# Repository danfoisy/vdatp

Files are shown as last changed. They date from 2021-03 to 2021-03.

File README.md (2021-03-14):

# VDATP
## Volumetric Display using an Acoustically Trapped Particle

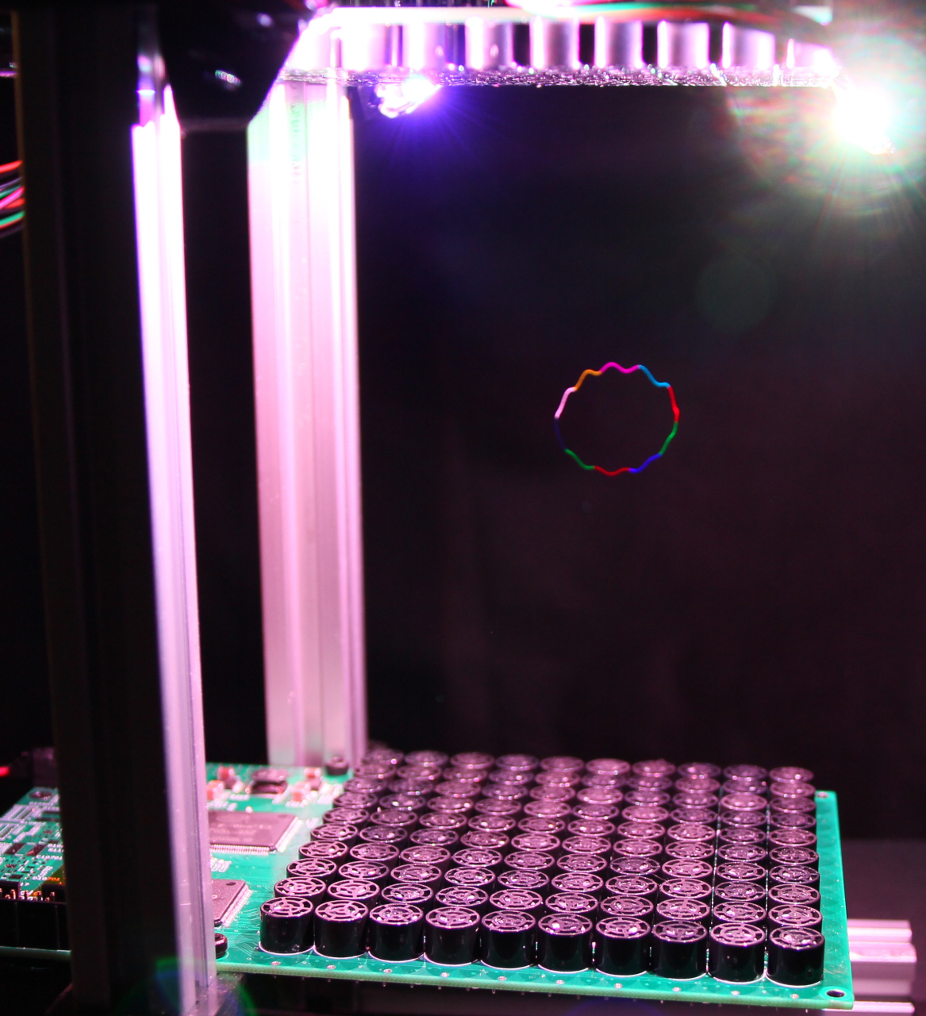
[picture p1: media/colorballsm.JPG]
VDATP video


This was such a fun project - I still giggle (maniacally) when watching this thing go.  There's something truly magical about watching something levitate in mid-air and then start zipping around so fast, you can't see it.  In any case, I hope these project files help someone!

Video: https://www.youtube.com/watch?v=hCC1C5KIeUA

References:
- PhysicsGirl acoustic levitator: https://www.youtube.com/watch?v=ABjRnSYw-4k
- Acoustic levitator Instructable: https://www.instructables.com/Acoustic-Levitator/
- University of Sussex video: https://www.youtube.com/watch?v=Tm8JRlJ1q50
- University of Sussex paper: http://sro.sussex.ac.uk/id/eprint/86930/

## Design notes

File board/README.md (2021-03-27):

# Board

Herein lives the Kicad schedmatics, PCB and BOM files.  If looking to replicate, I highly recommend you look at `errata.txt` for a list of mistakes I made that should be fixed on the next spin of the board.

Some notes:
- SPI goes to all 4 FPGAs simultaneously.  MISO is not used
- there are jumpers in place to allow the board to operate with only one FPGA installed (and only 50 transducers) but to run both FPGAs, the following jumpers must be configured:
-- R122, R123, R124, R126, R127, R128 <= populated
-- R125, R129 <= not populated
-- R105, R111, R113 <= not populated
-- R112 <= populated
- Raspberry Pi W installed on top board only. Top board needs 5V DC/DC converter populated, leave unpopulated on bottom board
-- Rasberry Pi header soldered on backside of Pi 
- U101 and U102 are soldered on top board (note errata on U101). Only U101 populated on bottom board
-- only simple twisted pair required for each RS485 connection
- LEDs only connect on top board (populate LED drivers and connectors)
- each board requires a max of 2A at 24V. No power sequencing required
- to allow the config device to program the FPGAs
-- JP201/JP202 must be left unpopulated
-- JP11001/JP11002 must be cut and msel0/1 must be connected to ground with jumper
- each FPGA must have jumpers configured to tell it which transducers it is responsible for
-- top board: populate R11004
-- bottom board: populate R11003, R203, R204
- original ultrasonic transducer is no available on aliexpress but https://manorshi.en.alibaba.com/product/60248714908-801018150/Manorshi_10mm_40khz_piezo_ultrasonic_Transmitter_Receiver_sensor.html should work but I've not tested (make sure to order the transmitter version)
- distance between boards is not super critical - mine are set up 145mm apart but other distance work just as well
- FPGAs can be programmed with a USB blaster type device.  I use https://www.terasic.com.tw/cgi-bin/page/archive.pl?Language=English&No=46
-- all FPGAs get the same program
- the transducers have a polarity marked on them - but don't trust the markings as they are wrong much of the time.  As well, I've been informed that there are phase discrepancies inherent in most of these cheap transducers.  I corrected for polarity errors by testing each transducer individually but did not correct for phase errors - this may be the cause of some of the distortions I saw.  I did check for these phase discrepancies and found a maximum of about 3% phase error across the transducers.  I don't know if this is enough to cause serious distortions but it may be worthwhile for someone to investigate.  If this is of concern, a simple LUT can be implemented to compensate for these errors on a transducer by transducer basis
- running these boards at 15V causes the drivers to get really hot - I suggest running them at 10V.

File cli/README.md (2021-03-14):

# CLI

This code runs on a Raspberry Pi and provides a command line interface to the FPGAs.  It sets up SPI0 at 500kHz and waits for the user to enter in commands.  No points for code cleanliness - this was purely for experimentation.

To compile the code:
`gcc -lm cli.c`

To run the code:
`./a.out [board separation distance] [radius]`
where:
```
board separation distance = the distance between the two boards in millimeters
radius = the radius under the ball that has enabled transducers.  This was used to try and reduce the distortions
```

I usually use: `./a.out 135 2000`

The most commonly used commands are as follows:
``` 
h   - moves the focus point to the home coordinates
z,a - increase/decrease Z coordinate
x,s - increase/decrease X coordinate
d,c - increase/decrease Y coordinate
o   - send profile to the FPGA FIFO
=,] - increase/decrease the time scaling factor
1,q - increase/decrease the X rotation angle
2,w - increase/decrease the Y rotation angle
3,e - increase/decrease the Z rotation angle
4,r - increase/decrease the scaling factor
+   - run a fly around animation
```

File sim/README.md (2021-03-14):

# SIM

This is the simulator code - a bit of a mess quite honestly but I tell myself that this was only for experimentation.  It was built for the last version QT5. You need to have CUDA installed and a CUDA/OpenGL GPU to make this work.

You can rotate the display by clicking and dragging.  The three sliders to the immediate right of the display control the viewing slice and the radio buttons set which slice is being display (or none).  `Pt Sz` changes the point size for each voxel, `Min Val` sets any voxels below the set value invisible and `Max Val` adjusts the overall scaling of the values.

Below the display are controls to animate or move the motion of the focus point.

The controls at the bottom marked `Color`, `Phase/Position` and `test` are used to communicate with the PI over a TCP/IP channel and send commands to move the focus point.

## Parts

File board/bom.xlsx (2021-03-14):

 |  |  |  |  | Ordered 2020/11/29
> C101, C104, C106, C201, C203, C204, C206, C209, C210, C213-C216, C219, C220, C223, C224, C227, C228, C231, C232, C235, C236, C239-C241, C247, C11001, C11003, C11004, C11006, C11009, C11010, C11013-C11016, C11019, C11020, C11023, C11024, C11027, C11028, C11031, C11032, C11035, C11036, C11039-C11041, C11047 | 4.7uF | Capacitor_SMD:C_0603_1608Metric | 1276-1044-1-ND | 51 | 100
> C102, C103, C105, C107, C202, C205, C207, C208, C211, C212, C217, C218, C221, C222, C225, C226, C229, C230, C233, C234, C237, C238, C242-C246, C248-C251, C307-C310, C316, C317, C11002, C11005, C11007, C11008, C11011, C11012, C11017, C11018, C11021, C11022, C11025, C11026, C11029, C11030, C11033, C11034, C11037, C11038, C11042-C11046, C11048-C11051 | 0.1uF | Capacitor_SMD:C_0402_1005Metric | 478-11507-1-ND | 64 | 130
> C301, C302 | 10uF,50V | Resistor_SMD:R_1210_3225Metric | 587-5961-1-ND | 2 | 4
> C304-C306, C315 | 22uF,35V | Capacitor_SMD:C_1210_3225Metric | 587-5853-1-ND | 4 | 10
> C311-C314, C318, C319 | 22uF | Capacitor_SMD:C_1210_3225Metric | 1276-1851-1-ND | 6 | 12
> C601, C701, C801, C901, C1001, C1101, C1201, C1301, C1401, C1501, C1601, C1701, C1801, C1901, C2001, C2101, C2201, C2301, C2401, C2501, C2601, C2701, C2801, C2901, C3001, C3101, C3201, C3301, C3401, C3501, C3601, C3701, C3801, C3901, C4001, C4101, C4201, C4301, C4401, C4501, C4601, C4701, C4801, C4901, C5001, C5101, C5201, C5301, C5401, C5501, C5601, C5701, C5801, C5901, C6001, C6101, C6201, C6301, C6401, C6501, C6601, C6701, C6801, C6901, C7001, C7101, C7201, C7301, C7401, C7501, C7601, C7701, C7801, C7901, C8001, C8101, C8201, C8301, C8401, C8501, C8601, C8701, C8801, C8901, C9001, C9101, C9201, C9301, C9401, C9501, C9601, C9701, C9801, C9901, C10001, C10101, C10201, C10301, C10401, C10501, C10702, C10802, C10902 | 4.7uF, 35V | Capacitor_SMD:C_1206_3216Metric | 587-3368-1-ND | 103 | 106
> C602, C702, C802, C902, C1002, C1102, C1202, C1302, C1402, C1502, C1602, C1702, C1802, C1902, C2002, C2102, C2202, C2302, C2402, C2502, C2602, C2702, C2802, C2902, C3002, C3102, C3202, C3302, C3402, C3502, C3602, C3702, C3802, C3902, C4002, C4102, C4202, C4302, C4402, C4502, C4602, C4702, C4802, C4902, C5002, C5102, C5202, C5302, C5402, C5502, C5602, C5702, C5802, C5902, C6002, C6102, C6202, C6302, C6402, C6502, C6602, C6702, C6802, C6902, C7002, C7102, C7202, C7302, C7402, C7502, C7602, C7702, C7802, C7902, C8002, C8102, C8202, C8302, C8402, C8502, C8602, C8702, C8802, C8902, C9002, C9102, C9202, C9302, C9402, C9502, C9602, C9702, C9802, C9902, C10002, C10102, C10202, C10302, C10402, C10502 | 0.1uF, 35V | Capacitor_SMD:C_0805_2012Metric | 587-3364-1-ND | 100 | 100
> C10701, C10801, C10901 | 1uF, 16V | Capacitor_SMD:C_0805_2012Metric | 587-4873-1-ND | 3 | 6
> D10701, D10801, D10901 | 2A, 100V | holo:DO-220A | SS2PH10-M3/84AGICT-ND | 3 | 6
> FB201, FB202, FB11001, FB11002 | 300R | Resistor_SMD:R_0402_1005Metric | 535-12548-1-ND | 4 | 10
J101 | JTAG | Connector_PinHeader_2.54mm:PinHeader_2x05_P2.54mm_Vertical_Shrouded | 732-2094-ND | 1 | 2
J102 | Comms | Connector_Hirose:Hirose_DF13-08P-1.25DS_1x08_P1.25mm_Horizontal | H2205-ND | 1 | 2
 |  |  | H2185-ND | 1 | 2
J301 | Power | Connector_Molex:Molex_70555_RA_1x02_P2.54 | WM14786 | 1 | 2
 |  |  | WM2900-ND | 1 | 2
> J10601-J10604 | Screw_Terminal_01x06 | Connector_Hirose:Hirose_DF13-06P-1.25DS_1x06_P1.25mm_Horizontal | H2203-ND | 4 | 8
 |  |  | H2183-ND | 4 | 8
L301 | 2.0uH | holo:NR8040 | 587-1997-1-ND | 1 | 2
L302 | 3.6uH | holo:NR8040 | 587-1998-1-ND | 1 | 2
L303 | 4.7uH | holo:NR8040 | 587-1999-1-ND | 1 | 2
> L10701, L10801 | 11.5uH | holo:SRR6038 | SRR6038-120YCT-ND | 2 | 3
L10901 | 18uH | holo:SRR6038 | SRR6038-180YCT-ND | 1 | -
> LS601, LS701, LS801, LS901, LS1001, LS1101, LS1201, LS1301, LS1401, LS1501, LS1601, LS1701, LS1801, LS1901, LS2001, LS2101, LS2201, LS2301, LS2401, LS2501, LS2601, LS2701, LS2801, LS2901, LS3001, LS3101, LS3201, LS3301, LS3401, LS3501, LS3601, LS3701, LS3801, LS3901, LS4001, LS4101, LS4201, LS4301, LS4401, LS4501, LS4601, LS4701, LS4801, LS4901, LS5001, LS5101, LS5201, LS5301, LS5401, LS5501, LS5601, LS5701, LS5801, LS5901, LS6001, LS6101, LS6201, LS6301, LS6401, LS6501, LS6601, LS6701, LS6801, LS6901, LS7001, LS7101, LS7201, LS7301, LS7401, LS7501, LS7601, LS7701, LS7801, LS7901, LS8001, LS8101, LS8201, LS8301, LS8401, LS8501, LS8601, LS8701, LS8801, LS8901, LS9001, LS9101, LS9201, LS9301, LS9401, LS9501, LS9601, LS9701, LS9801, LS9901, LS10001, LS10101, LS10201, LS10301, LS10401, LS10501 | Speaker_Ultrasound | holo:MSO-P1040H07T | stock | 100 | -
PS301 | OKI-T36W-W40 | holo:OKI-T-36W-W40 | 811-3132-1-ND | 1 | 2
R101 | 330R | Resistor_SMD:R_0402_1005Metric | 541-3996-1-ND | 1 | 10
R103 | 1.0K | Resistor_SMD:R_0402_1005Metric | A127319CT-ND | 1 | 10
> R102, R104, R201-R207, R11001-R11007 | 10K | Resistor_SMD:R_0402_1005Metric | RMCF0402JT10K0CT | 16 | 32
R105 | 0R | Resistor_SMD:R_0402_1005Metric | ~ | 1 | 10
R106 | 0R | Jumper:SolderJumper-2_P1.3mm_Open_TrianglePad1.0x1.5mm | ~ | 1 | -
> R107-R110 | 100R | Resistor_SMD:R_0402_1005Metric | A127223CT-ND | 4 | 20
> R208, R11008 | 24R9 | Resistor_SMD:R_0402_1005Metric | 2037-PFR05S-24R9-FNHCT-ND | 2 | 10
R301 | 52R21 | Resistor_SMD:R_0603_1608Metric | RMCF0603FT26R1CT-ND | 1 | 10
> R302, R303, R309 | 100K | Resistor_SMD:R_0402_1005Metric | RMCS0402JT100KCT-ND | 3 | 10
R304 | 47K | Resistor_SMD:R_0402_1005Metric | 541-3966-1-ND | 1 | 10
R305 | 5.0K | Resistor_SMD:R_0402_1005Metric | 541-3972-1-ND | 1 | 10
R306 | 10.31K | Resistor_SMD:R_0402_1005Metric | RR12P10.2KDCT-ND | 1 | 2
> R307, R310 | 75K | Resistor_SMD:R_0402_1005Metric | 541-5078-1-ND | 2 | 10
R308 | 27.6K | Resistor_SMD:R_0402_1005Metric | CR0402-FX-27R4GLFCT-ND | 1 | 10
R311 | 14.46K | Resistor_SMD:R_0402_1005Metric | YAG2983CT-ND | 1 | 10
> R10701, R10801, R10901 | 40K | Resistor_SMD:R_0402_1005Metric | CR0402-FX-4022GLFCT-ND | 3
> R10702, R10802, R10902 | 8.9K | Resistor_SMD:R_0402_1005Metric | RMCF0402FT8K87CT-ND | 3 | 10
SBC401 | Raspberry_Pi_2_3 | Module:Raspberry_Pi_Zero_Socketed_THT_MountingHoles_SMT |  | 0 | 1
SW101 | SW_Push | Button_Switch_SMD:SW_SPST_KMR2 | CKN10246CT-ND | 0
U101 | AM26LV32CDR | Package_SO:SOIC-16_3.9x9.9mm_P1.27mm | 296-6794-1-ND | 1 | 2
U102 | AM26LV31 | Package_SO:SOIC-16_3.9x9.9mm_P1.27mm | 296-25912-1-ND | 1 | 1
> U201, U11001 | 10CL010YE144C8G | Package_QFP:EQFP-144-1EP_20x20mm_P0.5mm_EP6.7x6.7mm | 544-3578-ND | 2 | 2
> U202, U11002 | MIC5504-2.5YM5 | Package_TO_SOT_SMD:SOT-23-5 | 576-4880-1-ND | 2 | 4
> U203, U11003 | EPCQ16A | Package_SO:SOIC-8_3.9x4.9mm_P1.27mm | 544-3440-ND | 2 | 2
> U204, U11004 | S25FL128L | Package_SO:SOIC-8_5.275x5.275mm_P1.27mm | 428-4642-1-ND | 2 | 2
> U301-U303 | RT7263A | holo:SOP-EP-8_3.9x4.9mm_P1.27mm | 1028-1217-1-ND | 3 | 6
> U601, U701, U801, U901, U1001, U1101, U1201, U1301, U1401, U1501, U1601, U1701, U1801, U1901, U2001, U2101, U2201, U2301, U2401, U2501, U2601, U2701, U2801, U2901, U3001, U3101, U3201, U3301, U3401, U3501, U3601, U3701, U3801, U3901, U4001, U4101, U4201, U4301, U4401, U4501, U4601, U4701, U4801, U4901, U5001, U5101, U5201, U5301, U5401, U5501, U5601, U5701, U5801, U5901, U6001, U6101, U6201, U6301, U6401, U6501, U6601, U6701, U6801, U6901, U7001, U7101, U7201, U7301, U7401, U7501, U7601, U7701, U7801, U7901, U8001, U8101, U8201, U8301, U8401, U8501, U8601, U8701, U8801, U8901, U9001, U9101, U9201, U9301, U9401, U9501, U9601, U9701, U9801, U9901, U10001, U10101, U10201, U10301, U10401, U10501 | TC4428A | Package_SO:SO-8_3.9x4.9mm_P1.27mm | aliexpress | 100
> U10701, U10801, U10901 | LM3414 | Package_SO:SOIC-8-1EP_3.9x4.9mm_P1.27mm_EP2.35x2.35mm | LM3414HVMRX/NOPBCT-ND | 3 | 3
X101 | ASE-24.576MHz | holo:ASFL1 | ASFL1-24.576MHZ-L-T | 1 | 2

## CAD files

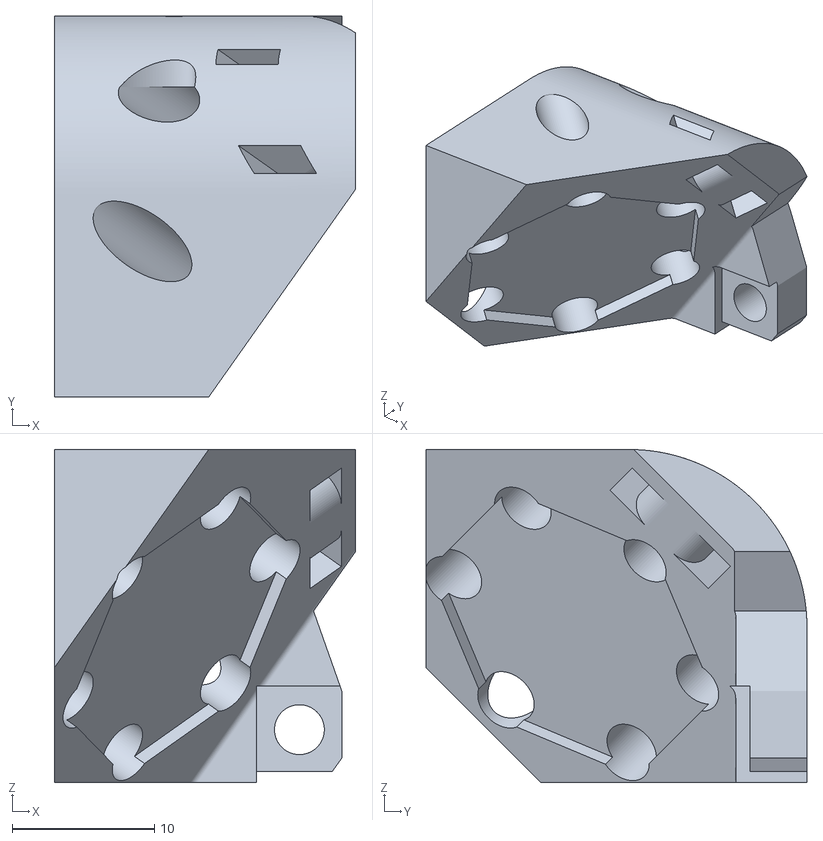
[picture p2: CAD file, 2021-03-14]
mech/LED mount1.stl
21.1 x 26.8 x 23.4

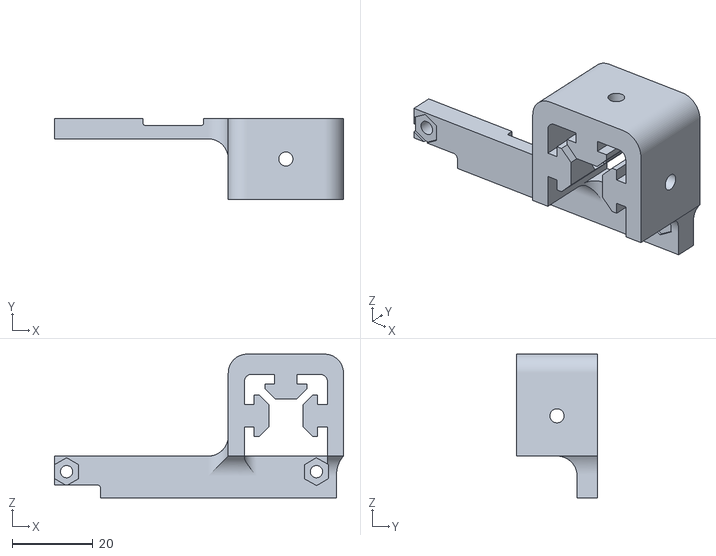
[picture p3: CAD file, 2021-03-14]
mech/bracket.stl
71.7 x 20.0 x 35.7

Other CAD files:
fpga/db/stp6_auto_stripped.stp
fpga/output_files/stp1.stp
fpga/stp1.stp
fpga/db/stp2_auto_stripped.stp
fpga/stp3.stp
fpga/db/stp4_auto_stripped.stp
fpga/stp9.stp
fpga/db/stp3_auto_stripped.stp
fpga/stp6.stp
fpga/db/stp1_auto_stripped.stp
fpga/stp2.stp
fpga/stp7.stp
fpga/stp4.stp

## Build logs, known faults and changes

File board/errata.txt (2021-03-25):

- add 0R on ncs/mosi/sck coming from U101 to allow using U101 at the same time as U102 for syncin signal
- as_* nets on FGPA2 are wrong on top page
- conf_done and nStatus lines should be connected together
- PD on LED enable lines
- silkscreen error R112/R131 switched

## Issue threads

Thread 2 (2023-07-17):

:-1: error: Unknown module(s) in QT: openglwidgets

AGNIVOTHIAGO, 2023-07-17:
I am having a windows 11, QT 5.0.2 and I really really need this simulation and I am trying to solve this one error for weeks now. I am completely new to QT rather its my first time in QT so I really need some help.
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

danfoisy, 2023-07-18:
This code was written with an older version of QT

Make is complaining that it can't find a dependency: openglwidgets

I think you can resolve the dependency by adding to line 2:
QT += openglwidgets

You can see that in the docs:
https://doc.qt.io/qt-6/qopenglwidget.html

Hope this helps

On Mon, Jul 17, 2023 at 1:01 PM AGNIVOTHIAGO ***@***.***>
wrote:

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

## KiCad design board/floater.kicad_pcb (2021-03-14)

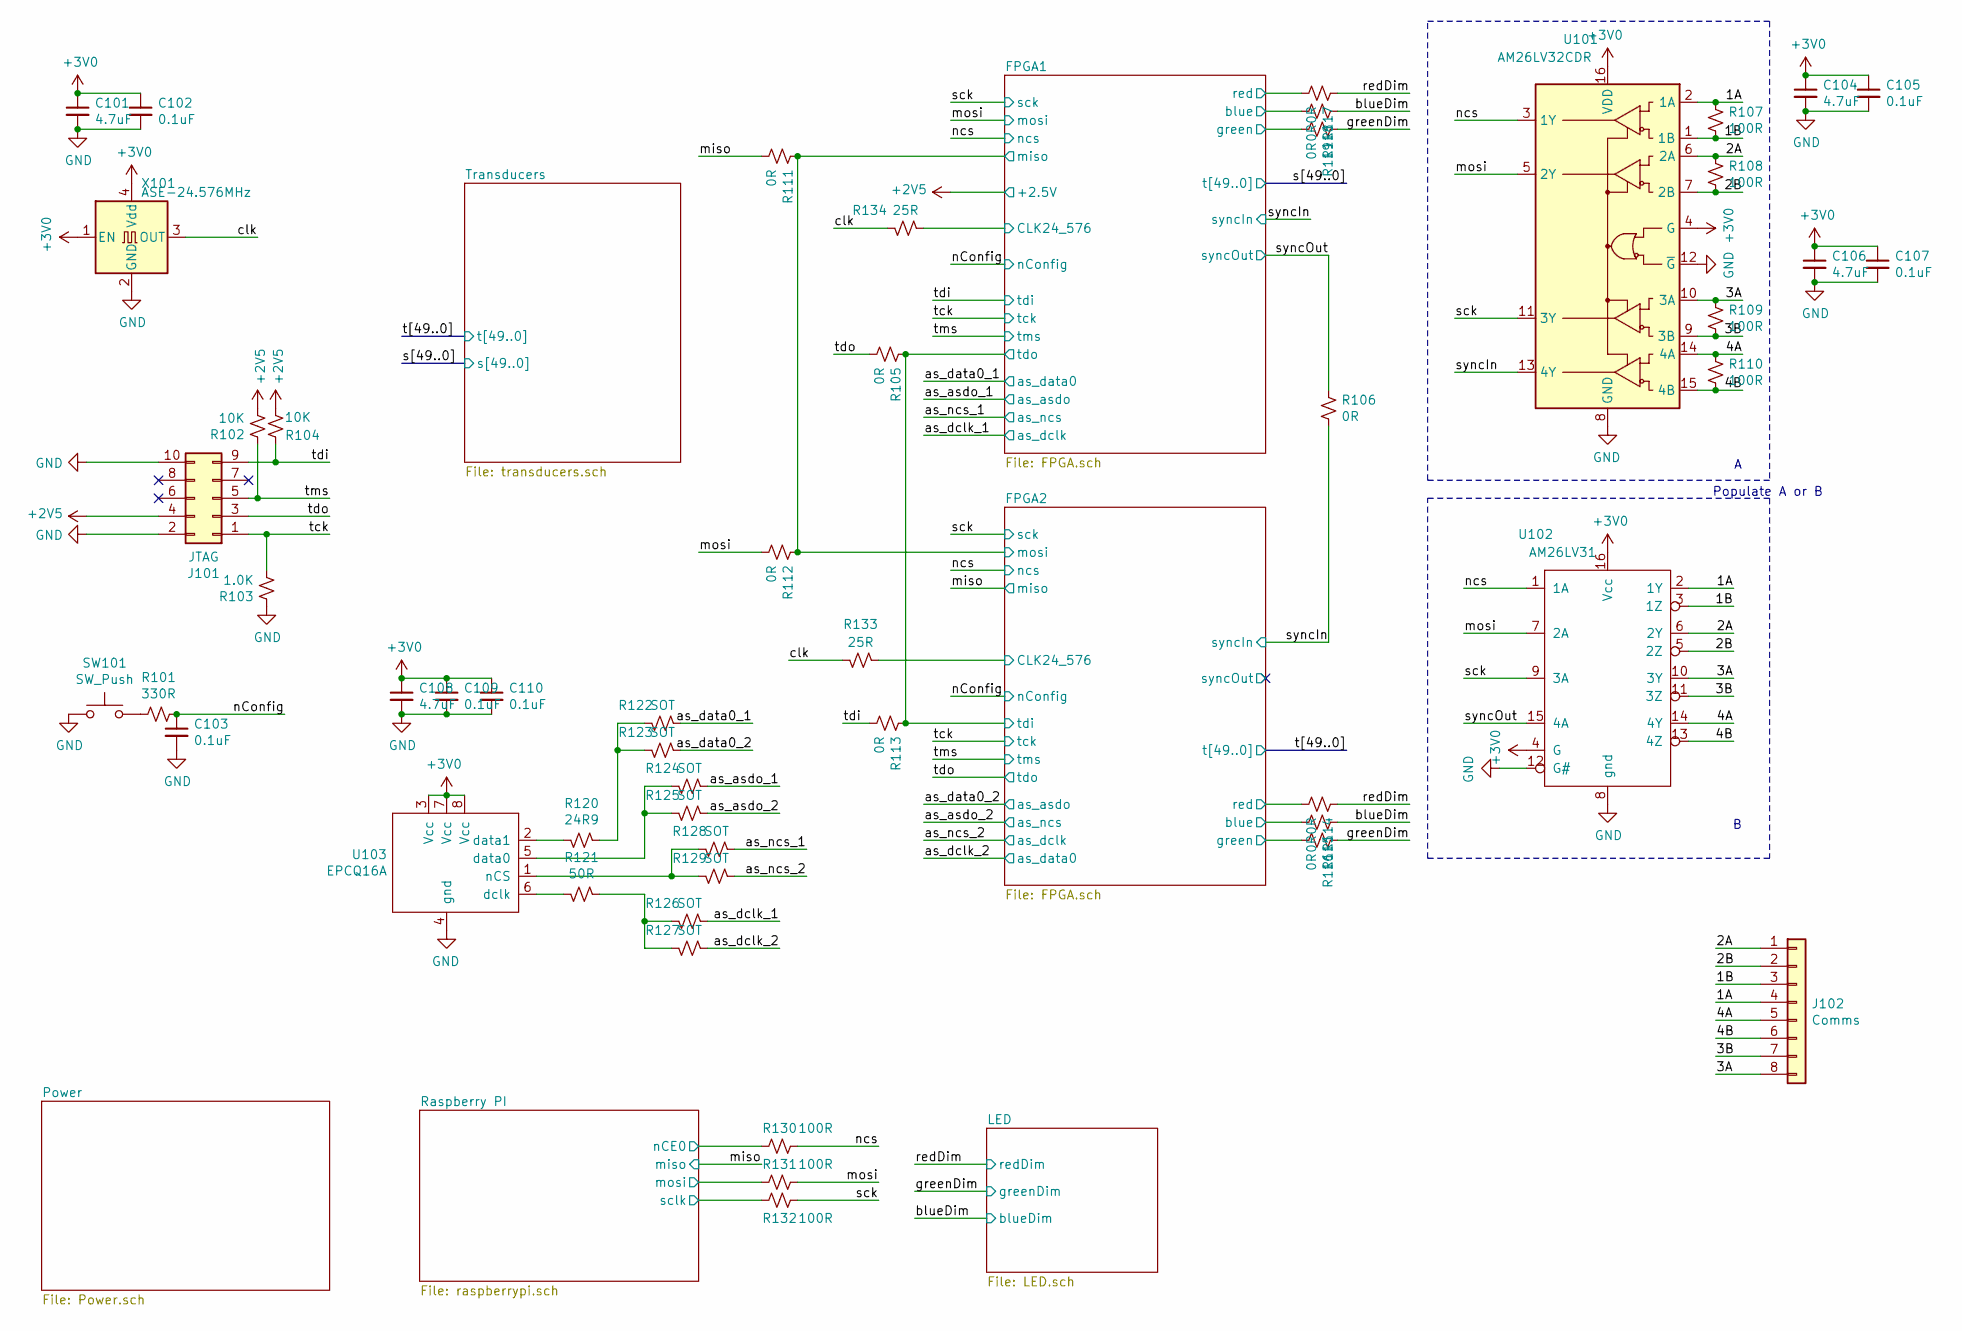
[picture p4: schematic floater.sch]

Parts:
C101, C104, C106, C108: 4.7uF; C_0603_1608Metric
C102, C103, C105, C107, C109, C110: 0.1uF; C_0402_1005Metric
J101: JTAG; PinHeader_2x05_P2.54mm_Vertical_Shrouded
J102: Comms; Hirose_DF13-08P-1.25DS_1x08_P1.25mm_Horizontal
R101: 330R; R_0402_1005Metric
R102, R104: 10K; R_0402_1005Metric
R103: 1.0K; R_0402_1005Metric
R105, R111, R112, R113, R114, R115, R116, R117, R118, R119: 0R; R_0402_1005Metric
R106: 0R; SolderJumper-2_P1.3mm_Open_TrianglePad1.0x1.5mm
R107, R108, R109, R110, R130, R131, R132: 100R; R_0402_1005Metric
R120: 24R9; R_0402_1005Metric
R121: 50R; R_0402_1005Metric
R122, R123, R124, R125, R126, R127, R128, R129: SOT; R_0402_1005Metric
R133, R134: 25R; R_0402_1005Metric
SW101: SW_Push; SW_SPST_KMR2
U101: AM26LV32CDR; SOIC-16_3.9x9.9mm_P1.27mm
U102: AM26LV31; SOIC-16_3.9x9.9mm_P1.27mm
U103: EPCQ16A; SOIC-8_3.9x4.9mm_P1.27mm
X101: ASE-24.576MHz; ASFL1

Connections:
+2V5: J101.4, R102.2, R104.2; also elsewhere on the board
+3V0: C101.1, C102.1, C104.1, C105.1, C106.1, C107.1, C108.1, C109.1, C110.1, U101.4 (G), U101.16 (VDD), U102.4 (G), U102.16 (Vcc), U103.3 (Vcc), U103.7 (Vcc), U103.8 (Vcc), X101.1 (EN), X101.4 (Vdd); also elsewhere on the board
/1A: J102.4, R107.1, U101.2 (1A), U102.2 (1Y)
/1B: J102.3, R107.2, U101.1 (1B), U102.3 (1Z)
/2A: J102.1, R108.1, U101.6 (2A), U102.6 (2Y)
/2B: J102.2, R108.2, U101.7 (2B), U102.5 (2Z)
/3A: J102.8, R109.1, U101.10 (3A), U102.10 (3Y)
/3B: J102.7, R109.2, U101.9 (3B), U102.11 (3Z)
/4A: J102.5, R110.1, U101.14 (4A), U102.14 (4Y)
/4B: J102.6, R110.2, U101.15 (4B), U102.13 (4Z)
/FPGA1/CLK24_576: R134.2; also elsewhere on the board
/FPGA1/blue: R118.2; also elsewhere on the board
/FPGA1/green: R119.2; also elsewhere on the board
/FPGA1/miso: R111.1, R112.1; also elsewhere on the board
/FPGA1/red: R117.2; also elsewhere on the board
/FPGA2/CLK24_576: R133.2; also elsewhere on the board
/FPGA2/blue: R115.2; also elsewhere on the board
/FPGA2/green: R116.2; also elsewhere on the board
/FPGA2/red: R114.2; also elsewhere on the board
/FPGA2/tdi: R105.1, R113.1; also elsewhere on the board
/Raspberry PI/mosi: R131.2; also elsewhere on the board
/Raspberry PI/nCE0: R130.2; also elsewhere on the board
/Raspberry PI/sclk: R132.2; also elsewhere on the board
/as_asdo_1: R124.2; also elsewhere on the board
/as_asdo_2: R125.2; also elsewhere on the board
/as_data0_1: R122.2; also elsewhere on the board
/as_data0_2: R123.2; also elsewhere on the board
/as_dclk_1: R126.2; also elsewhere on the board
/as_dclk_2: R127.2; also elsewhere on the board
/as_ncs_1: R128.2; also elsewhere on the board
/as_ncs_2: R129.2; also elsewhere on the board
/blueDim: R115.1, R118.1; also elsewhere on the board
/clk: R133.1, R134.1, X101.3 (OUT)
/greenDim: R116.1, R119.1; also elsewhere on the board
/miso: R111.2; also elsewhere on the board
/mosi: R112.2, R131.1, U101.5 (2Y), U102.7 (2A); also elsewhere on the board
/nConfig: C103.1, R101.2; also elsewhere on the board
/ncs: R130.1, U101.3 (1Y), U102.1 (1A); also elsewhere on the board
/redDim: R114.1, R117.1; also elsewhere on the board
/sck: R132.1, U101.11 (3Y), U102.9 (3A); also elsewhere on the board
/syncIn: R106.2, U101.13 (4Y); also elsewhere on the board
/syncOut: R106.1, U102.15 (4A); also elsewhere on the board
/tck: J101.1, R103.2; also elsewhere on the board
/tdi: J101.9, R104.1, R113.2; also elsewhere on the board
/tdo: J101.3, R105.2; also elsewhere on the board
/tms: J101.5, R102.1; also elsewhere on the board
GND: C101.2, C102.2, C103.2, C104.2, C105.2, C106.2, C107.2, C108.2, C109.2, C110.2, J101.2, J101.10, R103.1, SW101.1, U101.8 (GND), U101.12 (~G), U102.8 (gnd), U102.12 (G#), U103.4 (gnd), X101.2 (GND); also elsewhere on the board
unnamed: R101.1, SW101.2
unnamed: R120.1, U103.2 (data1)
unnamed: R120.2, R122.1, R123.1
unnamed: R121.1, U103.6 (dclk)
unnamed: R121.2, R126.1, R127.1
unnamed: R124.1, R125.1, U103.5 (data0)
unnamed: R128.1, R129.1, U103.1 (nCS)

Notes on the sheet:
Populate A or B

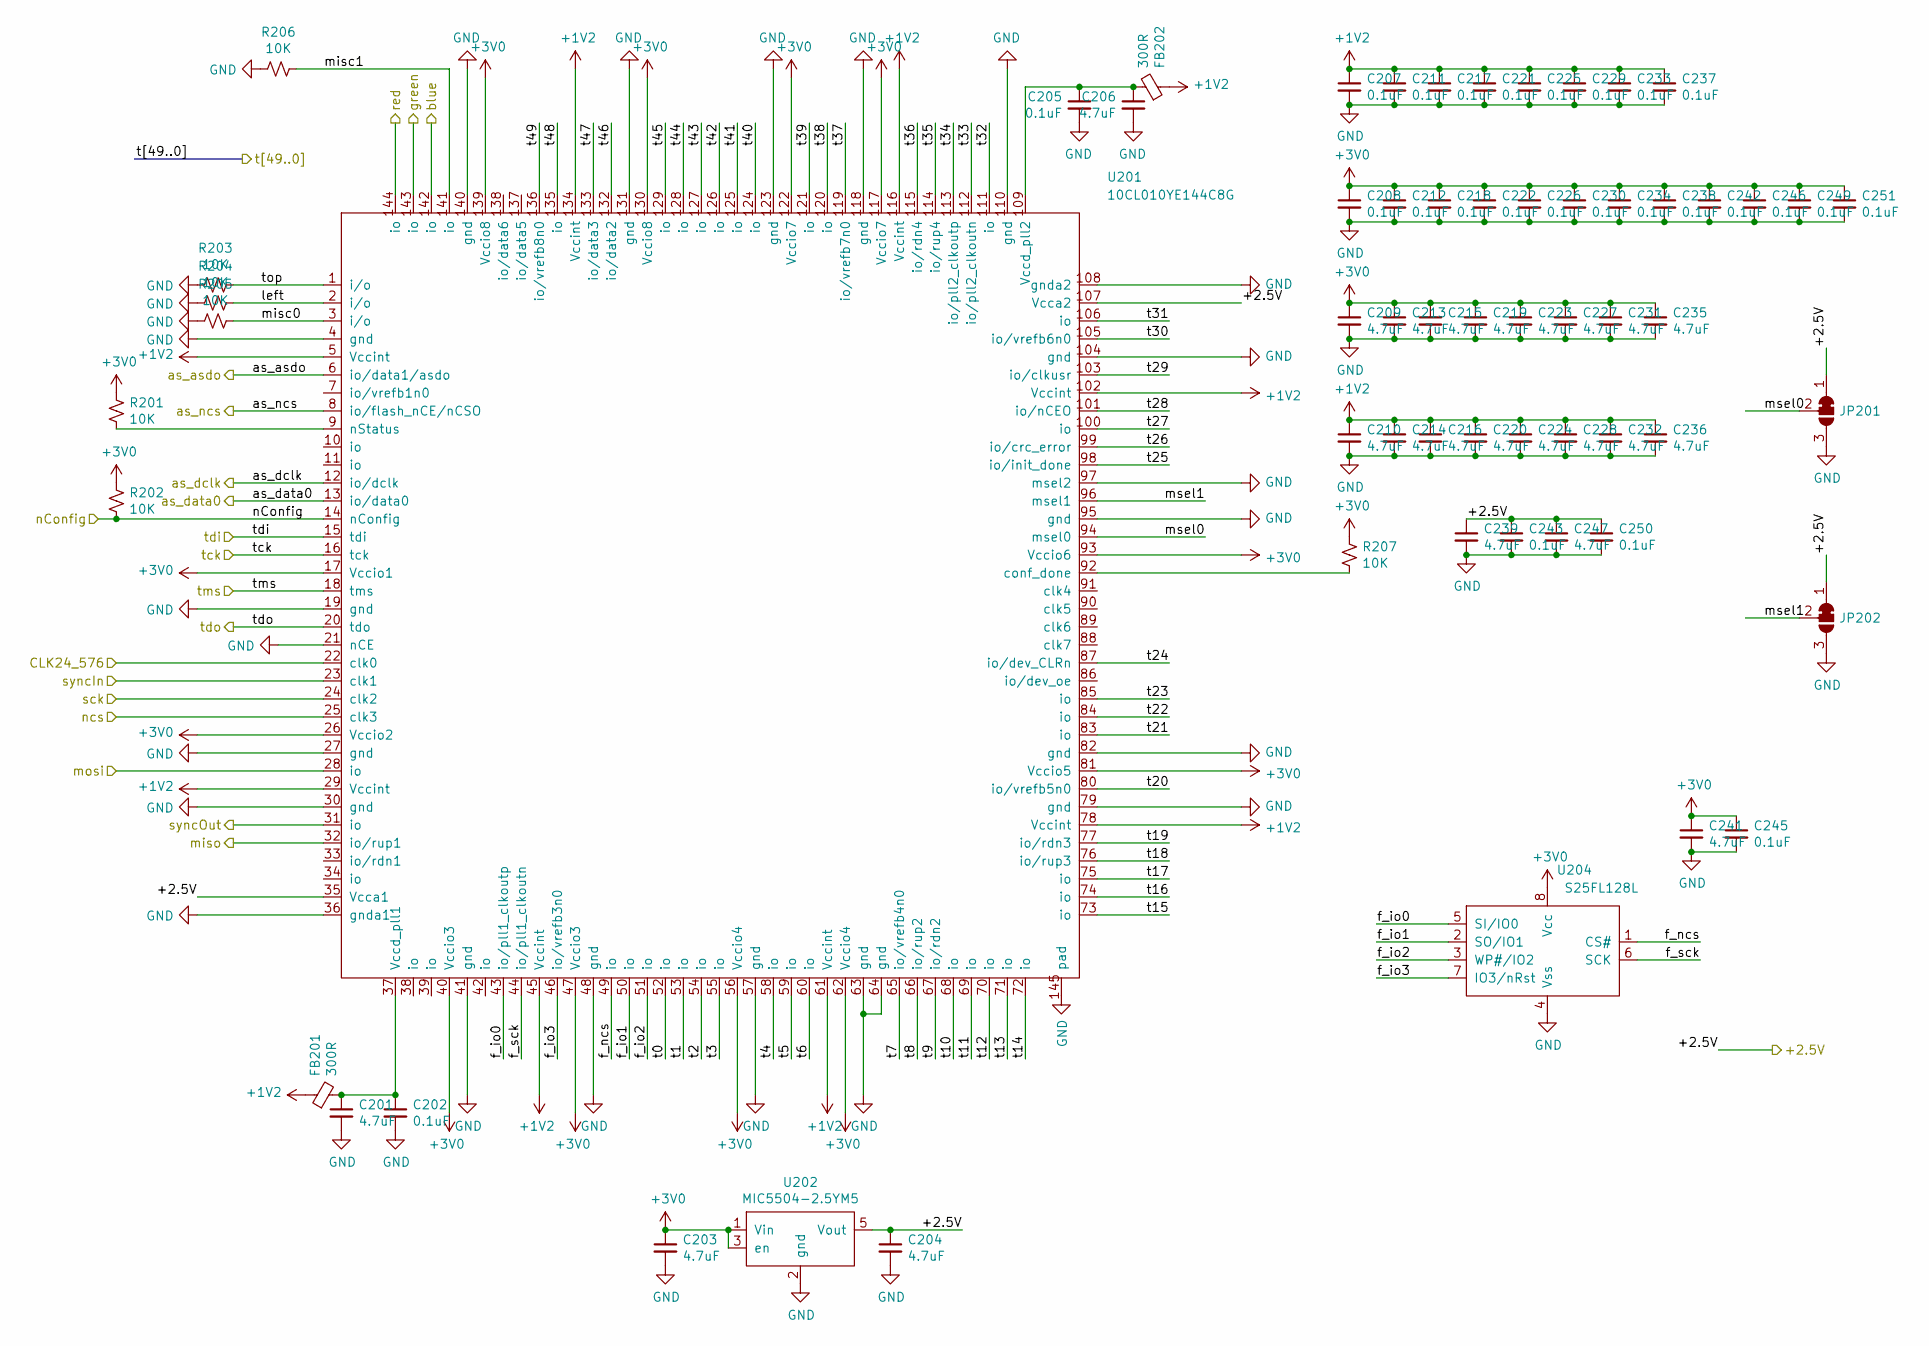
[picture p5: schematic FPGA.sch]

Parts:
C201, C203, C204, C206, C209, C210, C213, C214, C215, C216, C219, C220, C223, C224, C227, C228, C231, C232, C235, C236, C239, C247, C11041: 4.7uF; C_0603_1608Metric
C202, C205, C207, C208, C211, C212, C217, C218, C221, C222, C225, C226, C229, C230, C233, C234, C237, C238, C242, C243, C246, C249, C250, C251, C11045: 0.1uF; C_0402_1005Metric
FB201, FB202: 300R; R_0402_1005Metric
JP201, JP202: SolderJumper_3_Bridged12; SolderJumper-3_bridged12
R201, R202, R203, R204, R205, R206, R207: 10K; R_0402_1005Metric
U201: 10CL010YE144C8G; EQFP-144-1EP_20x20mm_P0.5mm_EP6.7x6.7mm
U202: MIC5504-2.5YM5; SOT-23-5
U204: S25FL128L; SOIC-8_5.275x5.275mm_P1.27mm

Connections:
+1V2: C207.1, C210.1, C211.1, C214.1, C216.1, C217.1, C220.1, C221.1, C224.1, C225.1, C228.1, C229.1, C232.1, C233.1, C236.1, C237.1, FB201.1, FB202.1, U201.5 (Vccint), U201.29 (Vccint), U201.45 (Vccint), U201.61 (Vccint), U201.78 (Vccint), U201.102 (Vccint), U201.116 (Vccint), U201.134 (Vccint); also elsewhere on the board
+2V5: C204.1, C239.1, C243.1, C247.1, C250.1, JP201.1 (A), JP202.1 (A), U201.35 (Vcca1), U201.107 (Vcca2), U202.5 (Vout); also elsewhere on the board
+3V0: C203.1, C208.1, C209.1, C212.1, C213.1, C215.1, C218.1, C219.1, C222.1, C223.1, C226.1, C227.1, C230.1, C231.1, C234.1, C235.1, C238.1, C242.1, C246.1, C249.1, C251.1, C11041.1, C11045.1, R201.2, R202.2, R207.2, U201.17 (Vccio1), U201.26 (Vccio2), U201.40 (Vccio3), U201.47 (Vccio3), U201.56 (Vccio4), U201.62 (Vccio4), U201.81 (Vccio5), U201.93 (Vccio6), U201.117 (Vccio7), U201.122 (Vccio7), U201.130 (Vccio8), U201.139 (Vccio8), U202.1 (Vin), U202.3 (en), U204.8 (Vcc); also elsewhere on the board
/FPGA1/CLK24_576: U201.22 (clk0); also elsewhere on the board
/FPGA1/blue: U201.142 (io); also elsewhere on the board
/FPGA1/f_io0: U201.43 (io/pll1_clkoutp), U204.5 (SI/IO0)
/FPGA1/f_io1: U201.50 (io), U204.2 (SO/IO1)
/FPGA1/f_io2: U201.51 (io), U204.3 (WP#/IO2)
/FPGA1/f_io3: U201.46 (io/vrefb3n0), U204.7 (IO3/nRst)
/FPGA1/f_ncs: U201.49 (io), U204.1 (CS#)
/FPGA1/f_sck: U201.44 (io/pll1_clkoutn), U204.6 (SCK)
/FPGA1/green: U201.143 (io); also elsewhere on the board
/FPGA1/left: R204.2, U201.2 (i/o)
/FPGA1/misc0: R205.2, U201.3 (i/o)
/FPGA1/misc1: R206.2, U201.141 (io)
/FPGA1/miso: U201.32 (io/rup1); also elsewhere on the board
/FPGA1/msel0: JP201.2 (C), U201.94 (msel0)
/FPGA1/msel1: JP202.2 (C), U201.96 (msel1)
/FPGA1/red: U201.144 (io); also elsewhere on the board
/FPGA1/top: R203.2, U201.1 (i/o)
/FPGA2/tdi: U201.20 (tdo); also elsewhere on the board
/Transducers/s0: U201.52 (io); also elsewhere on the board
/Transducers/s1: U201.53 (io); also elsewhere on the board
/Transducers/s2: U201.54 (io); also elsewhere on the board
/Transducers/s3: U201.55 (io); also elsewhere on the board
/Transducers/s4: U201.58 (io); also elsewhere on the board
/Transducers/s5: U201.59 (io); also elsewhere on the board
/Transducers/s6: U201.60 (io); also elsewhere on the board
/Transducers/s7: U201.65 (io/vrefb4n0); also elsewhere on the board
/Transducers/s8: U201.66 (io/rup2); also elsewhere on the board
/Transducers/s9: U201.67 (io/rdn2); also elsewhere on the board
/Transducers/s10: U201.68 (io); also elsewhere on the board
/Transducers/s11: U201.69 (io); also elsewhere on the board
/Transducers/s12: U201.70 (io); also elsewhere on the board
/Transducers/s13: U201.71 (io); also elsewhere on the board
/Transducers/s14: U201.72 (io); also elsewhere on the board
/Transducers/s15: U201.73 (io); also elsewhere on the board
/Transducers/s16: U201.74 (io); also elsewhere on the board
/Transducers/s17: U201.75 (io); also elsewhere on the board
/Transducers/s18: U201.76 (io/rup3); also elsewhere on the board
/Transducers/s19: U201.77 (io/rdn3); also elsewhere on the board
/Transducers/s20: U201.80 (io/vrefb5n0); also elsewhere on the board
/Transducers/s21: U201.83 (io); also elsewhere on the board
/Transducers/s22: U201.84 (io); also elsewhere on the board
/Transducers/s23: U201.85 (io); also elsewhere on the board
/Transducers/s24: U201.87 (io/dev_CLRn); also elsewhere on the board
/Transducers/s25: U201.98 (io/init_done); also elsewhere on the board
/Transducers/s26: U201.99 (io/crc_error); also elsewhere on the board
/Transducers/s27: U201.100 (io); also elsewhere on the board
/Transducers/s28: U201.101 (io/nCEO); also elsewhere on the board
/Transducers/s29: U201.103 (io/clkusr); also elsewhere on the board
/Transducers/s30: U201.105 (io/vrefb6n0); also elsewhere on the board
/Transducers/s31: U201.106 (io); also elsewhere on the board
/Transducers/s32: U201.111 (io); also elsewhere on the board
/Transducers/s33: U201.112 (io/pll2_clkoutn); also elsewhere on the board
/Transducers/s34: U201.113 (io/pll2_clkoutp); also elsewhere on the board
/Transducers/s35: U201.114 (io/rup4); also elsewhere on the board
/Transducers/s36: U201.115 (io/rdn4); also elsewhere on the board
/Transducers/s37: U201.119 (io/vrefb7n0); also elsewhere on the board
/Transducers/s38: U201.120 (io); also elsewhere on the board
/Transducers/s39: U201.121 (io); also elsewhere on the board
/Transducers/s40: U201.124 (io); also elsewhere on the board
/Transducers/s41: U201.125 (io); also elsewhere on the board
/Transducers/s42: U201.126 (io); also elsewhere on the board
/Transducers/s43: U201.127 (io); also elsewhere on the board
/Transducers/s44: U201.128 (io); also elsewhere on the board
/Transducers/s45: U201.129 (io); also elsewhere on the board
/Transducers/s46: U201.132 (io/data2); also elsewhere on the board
/Transducers/s47: U201.133 (io/data3); also elsewhere on the board
/Transducers/s48: U201.135 (io); also elsewhere on the board
/Transducers/s49: U201.136 (io/vrefb8n0); also elsewhere on the board
/as_asdo_1: U201.6 (io/data1/asdo); also elsewhere on the board
/as_data0_1: U201.13 (io/data0); also elsewhere on the board
/as_dclk_1: U201.12 (io/dclk); also elsewhere on the board
/as_ncs_1: U201.8 (io/flash_nCE/nCSO); also elsewhere on the board
/mosi: U201.28 (io); also elsewhere on the board
/nConfig: R202.1, U201.14 (nConfig); also elsewhere on the board
/ncs: U201.25 (clk3); also elsewhere on the board
/sck: U201.24 (clk2); also elsewhere on the board
/syncIn: U201.23 (clk1); also elsewhere on the board
/syncOut: U201.31 (io); also elsewhere on the board
/tck: U201.16 (tck); also elsewhere on the board
/tdi: U201.15 (tdi); also elsewhere on the board
/tms: U201.18 (tms); also elsewhere on the board
GND: C201.2, C202.2, C203.2, C204.2, C205.2, C206.2, C207.2, C208.2, C209.2, C210.2, C211.2, C212.2, C213.2, C214.2, C215.2, C216.2, C217.2, C218.2, C219.2, C220.2, C221.2, C222.2, C223.2, C224.2, C225.2, C226.2, C227.2, C228.2, C229.2, C230.2, C231.2, C232.2, C233.2, C234.2, C235.2, C236.2, C237.2, C238.2, C239.2, C242.2, C243.2, C246.2, C247.2, C249.2, C250.2, C251.2, C11041.2, C11045.2, JP201.3 (B), JP202.3 (B), R203.1, R204.1, R205.1, R206.1, U201.4 (gnd), U201.19 (gnd), U201.21 (nCE), U201.27 (gnd), U201.30 (gnd), U201.36 (gnda1), U201.41 (gnd), U201.48 (gnd), U201.57 (gnd), U201.63 (gnd), U201.64 (gnd), U201.79 (gnd), U201.82 (gnd), U201.95 (gnd), U201.97 (msel2), U201.104 (gnd), U201.108 (gnda2), U201.110 (gnd), U201.118 (gnd), U201.123 (gnd), U201.131 (gnd), U201.140 (gnd), U201.145 (pad), U202.2 (gnd), U204.4 (Vss); also elsewhere on the board
unnamed: C201.1, C202.1, FB201.2, U201.37 (Vccd_pll1)
unnamed: C205.1, C206.1, FB202.2, U201.109 (Vccd_pll2)
unnamed: R201.1, U201.9 (nStatus)
unnamed: R207.1, U201.92 (conf_done)

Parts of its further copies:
C241, C11001, C11003, C11004, C11006, C11009, C11010, C11013, C11014, C11015, C11016, C11019, C11020, C11023, C11024, C11027, C11028, C11031, C11032, C11035, C11036, C11039, C11047: 4.7uF; C_0603_1608Metric
C245, C11002, C11005, C11007, C11008, C11011, C11012, C11017, C11018, C11021, C11022, C11025, C11026, C11029, C11030, C11033, C11034, C11037, C11038, C11042, C11043, C11046, C11049, C11050, C11051: 0.1uF; C_0402_1005Metric
FB11001, FB11002: 300R; R_0402_1005Metric
JP11001, JP11002: SolderJumper_3_Bridged12; SolderJumper-3_bridged12
R11001, R11002, R11003, R11004, R11005, R11006, R11007: 10K; R_0402_1005Metric
U11001: 10CL010YE144C8G; EQFP-144-1EP_20x20mm_P0.5mm_EP6.7x6.7mm
U11002: MIC5504-2.5YM5; SOT-23-5
U11004: S25FL128L; SOIC-8_5.275x5.275mm_P1.27mm

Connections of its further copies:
+1V2: C11007.1, C11010.1, C11011.1, C11014.1, C11016.1, C11017.1, C11020.1, C11021.1, C11024.1, C11025.1, C11028.1, C11029.1, C11032.1, C11033.1, C11036.1, C11037.1, FB11001.1, FB11002.1, U11001.5 (Vccint), U11001.29 (Vccint), U11001.45 (Vccint), U11001.61 (Vccint), U11001.78 (Vccint), U11001.102 (Vccint), U11001.116 (Vccint), U11001.134 (Vccint); also elsewhere on the board
+3V0: C241.1, C245.1, C11003.1, C11008.1, C11009.1, C11012.1, C11013.1, C11015.1, C11018.1, C11019.1, C11022.1, C11023.1, C11026.1, C11027.1, C11030.1, C11031.1, C11034.1, C11035.1, C11038.1, C11042.1, C11046.1, C11049.1, C11051.1, R11001.2, R11002.2, R11007.2, U11001.17 (Vccio1), U11001.26 (Vccio2), U11001.40 (Vccio3), U11001.47 (Vccio3), U11001.56 (Vccio4), U11001.62 (Vccio4), U11001.81 (Vccio5), U11001.93 (Vccio6), U11001.117 (Vccio7), U11001.122 (Vccio7), U11001.130 (Vccio8), U11001.139 (Vccio8), U11002.1 (Vin), U11002.3 (en), U11004.8 (Vcc); also elsewhere on the board
/FPGA1/miso: U11001.28 (io); also elsewhere on the board
/FPGA2/+2.5V: C11004.1, C11039.1, C11043.1, C11047.1, C11050.1, JP11001.1 (A), JP11002.1 (A), U11001.35 (Vcca1), U11001.107 (Vcca2), U11002.5 (Vout)
/FPGA2/CLK24_576: U11001.22 (clk0); also elsewhere on the board
/FPGA2/blue: U11001.142 (io); also elsewhere on the board
/FPGA2/f_io0: U11001.43 (io/pll1_clkoutp), U11004.5 (SI/IO0)
/FPGA2/f_io1: U11001.50 (io), U11004.2 (SO/IO1)
/FPGA2/f_io2: U11001.51 (io), U11004.3 (WP#/IO2)
/FPGA2/f_io3: U11001.46 (io/vrefb3n0), U11004.7 (IO3/nRst)
/FPGA2/f_ncs: U11001.49 (io), U11004.1 (CS#)
/FPGA2/f_sck: U11001.44 (io/pll1_clkoutn), U11004.6 (SCK)
/FPGA2/green: U11001.143 (io); also elsewhere on the board
/FPGA2/left: R11004.2, U11001.2 (i/o)
/FPGA2/misc0: R11005.2, U11001.3 (i/o)
/FPGA2/misc1: R11006.2, U11001.141 (io)
/FPGA2/msel0: JP11001.2 (C), U11001.94 (msel0)
/FPGA2/msel1: JP11002.2 (C), U11001.96 (msel1)
/FPGA2/red: U11001.144 (io); also elsewhere on the board
/FPGA2/syncOut: U11001.31 (io)
/FPGA2/t0: U11001.52 (io); also elsewhere on the board
/FPGA2/t1: U11001.53 (io); also elsewhere on the board
/FPGA2/t2: U11001.54 (io); also elsewhere on the board
/FPGA2/t3: U11001.55 (io); also elsewhere on the board
/FPGA2/t4: U11001.58 (io); also elsewhere on the board
/FPGA2/t5: U11001.59 (io); also elsewhere on the board
/FPGA2/t6: U11001.60 (io); also elsewhere on the board
/FPGA2/t7: U11001.65 (io/vrefb4n0); also elsewhere on the board
/FPGA2/t8: U11001.66 (io/rup2); also elsewhere on the board
/FPGA2/t9: U11001.67 (io/rdn2); also elsewhere on the board
/FPGA2/t10: U11001.68 (io); also elsewhere on the board
/FPGA2/t11: U11001.69 (io); also elsewhere on the board
/FPGA2/t12: U11001.70 (io); also elsewhere on the board
/FPGA2/t13: U11001.71 (io); also elsewhere on the board
/FPGA2/t14: U11001.72 (io); also elsewhere on the board
/FPGA2/t15: U11001.73 (io); also elsewhere on the board
/FPGA2/t16: U11001.74 (io); also elsewhere on the board
/FPGA2/t17: U11001.75 (io); also elsewhere on the board
/FPGA2/t18: U11001.76 (io/rup3); also elsewhere on the board
/FPGA2/t19: U11001.77 (io/rdn3); also elsewhere on the board
/FPGA2/t20: U11001.80 (io/vrefb5n0); also elsewhere on the board
/FPGA2/t21: U11001.83 (io); also elsewhere on the board
/FPGA2/t22: U11001.84 (io); also elsewhere on the board
/FPGA2/t23: U11001.85 (io); also elsewhere on the board
/FPGA2/t24: U11001.87 (io/dev_CLRn); also elsewhere on the board
/FPGA2/t25: U11001.98 (io/init_done); also elsewhere on the board
/FPGA2/t26: U11001.99 (io/crc_error); also elsewhere on the board
/FPGA2/t27: U11001.100 (io); also elsewhere on the board
/FPGA2/t28: U11001.101 (io/nCEO); also elsewhere on the board
/FPGA2/t29: U11001.103 (io/clkusr); also elsewhere on the board
/FPGA2/t30: U11001.105 (io/vrefb6n0); also elsewhere on the board
/FPGA2/t31: U11001.106 (io); also elsewhere on the board
/FPGA2/t32: U11001.111 (io); also elsewhere on the board
/FPGA2/t33: U11001.112 (io/pll2_clkoutn); also elsewhere on the board
/FPGA2/t34: U11001.113 (io/pll2_clkoutp); also elsewhere on the board
/FPGA2/t35: U11001.114 (io/rup4); also elsewhere on the board
/FPGA2/t36: U11001.115 (io/rdn4); also elsewhere on the board
/FPGA2/t37: U11001.119 (io/vrefb7n0); also elsewhere on the board
/FPGA2/t38: U11001.120 (io); also elsewhere on the board
/FPGA2/t39: U11001.121 (io); also elsewhere on the board
/FPGA2/t40: U11001.124 (io); also elsewhere on the board
/FPGA2/t41: U11001.125 (io); also elsewhere on the board
/FPGA2/t42: U11001.126 (io); also elsewhere on the board
/FPGA2/t43: U11001.127 (io); also elsewhere on the board
/FPGA2/t44: U11001.128 (io); also elsewhere on the board
/FPGA2/t45: U11001.129 (io); also elsewhere on the board
/FPGA2/t46: U11001.132 (io/data2); also elsewhere on the board
/FPGA2/t47: U11001.133 (io/data3); also elsewhere on the board
/FPGA2/t48: U11001.135 (io); also elsewhere on the board
/FPGA2/t49: U11001.136 (io/vrefb8n0); also elsewhere on the board
/FPGA2/tdi: U11001.15 (tdi); also elsewhere on the board
/FPGA2/top: R11003.2, U11001.1 (i/o)
/as_asdo_2: U11001.8 (io/flash_nCE/nCSO); also elsewhere on the board
/as_data0_2: U11001.6 (io/data1/asdo); also elsewhere on the board
/as_dclk_2: U11001.13 (io/data0); also elsewhere on the board
/as_ncs_2: U11001.12 (io/dclk); also elsewhere on the board
/miso: U11001.32 (io/rup1); also elsewhere on the board
/nConfig: R11002.1, U11001.14 (nConfig); also elsewhere on the board
/ncs: U11001.25 (clk3); also elsewhere on the board
/sck: U11001.24 (clk2); also elsewhere on the board
/syncIn: U11001.23 (clk1); also elsewhere on the board
/tck: U11001.16 (tck); also elsewhere on the board
/tdo: U11001.20 (tdo); also elsewhere on the board
/tms: U11001.18 (tms); also elsewhere on the board
GND: C241.2, C245.2, C11001.2, C11002.2, C11003.2, C11004.2, C11005.2, C11006.2, C11007.2, C11008.2, C11009.2, C11010.2, C11011.2, C11012.2, C11013.2, C11014.2, C11015.2, C11016.2, C11017.2, C11018.2, C11019.2, C11020.2, C11021.2, C11022.2, C11023.2, C11024.2, C11025.2, C11026.2, C11027.2, C11028.2, C11029.2, C11030.2, C11031.2, C11032.2, C11033.2, C11034.2, C11035.2, C11036.2, C11037.2, C11038.2, C11039.2, C11042.2, C11043.2, C11046.2, C11047.2, C11049.2, C11050.2, C11051.2, JP11001.3 (B), JP11002.3 (B), R11003.1, R11004.1, R11005.1, R11006.1, U11001.4 (gnd), U11001.19 (gnd), U11001.21 (nCE), U11001.27 (gnd), U11001.30 (gnd), U11001.36 (gnda1), U11001.41 (gnd), U11001.48 (gnd), U11001.57 (gnd), U11001.63 (gnd), U11001.64 (gnd), U11001.79 (gnd), U11001.82 (gnd), U11001.95 (gnd), U11001.97 (msel2), U11001.104 (gnd), U11001.108 (gnda2), U11001.110 (gnd), U11001.118 (gnd), U11001.123 (gnd), U11001.131 (gnd), U11001.140 (gnd), U11001.145 (pad), U11002.2 (gnd), U11004.4 (Vss); also elsewhere on the board
unnamed: C11001.1, C11002.1, FB11001.2, U11001.37 (Vccd_pll1)
unnamed: C11005.1, C11006.1, FB11002.2, U11001.109 (Vccd_pll2)
unnamed: R11001.1, U11001.9 (nStatus)
unnamed: R11007.1, U11001.92 (conf_done)

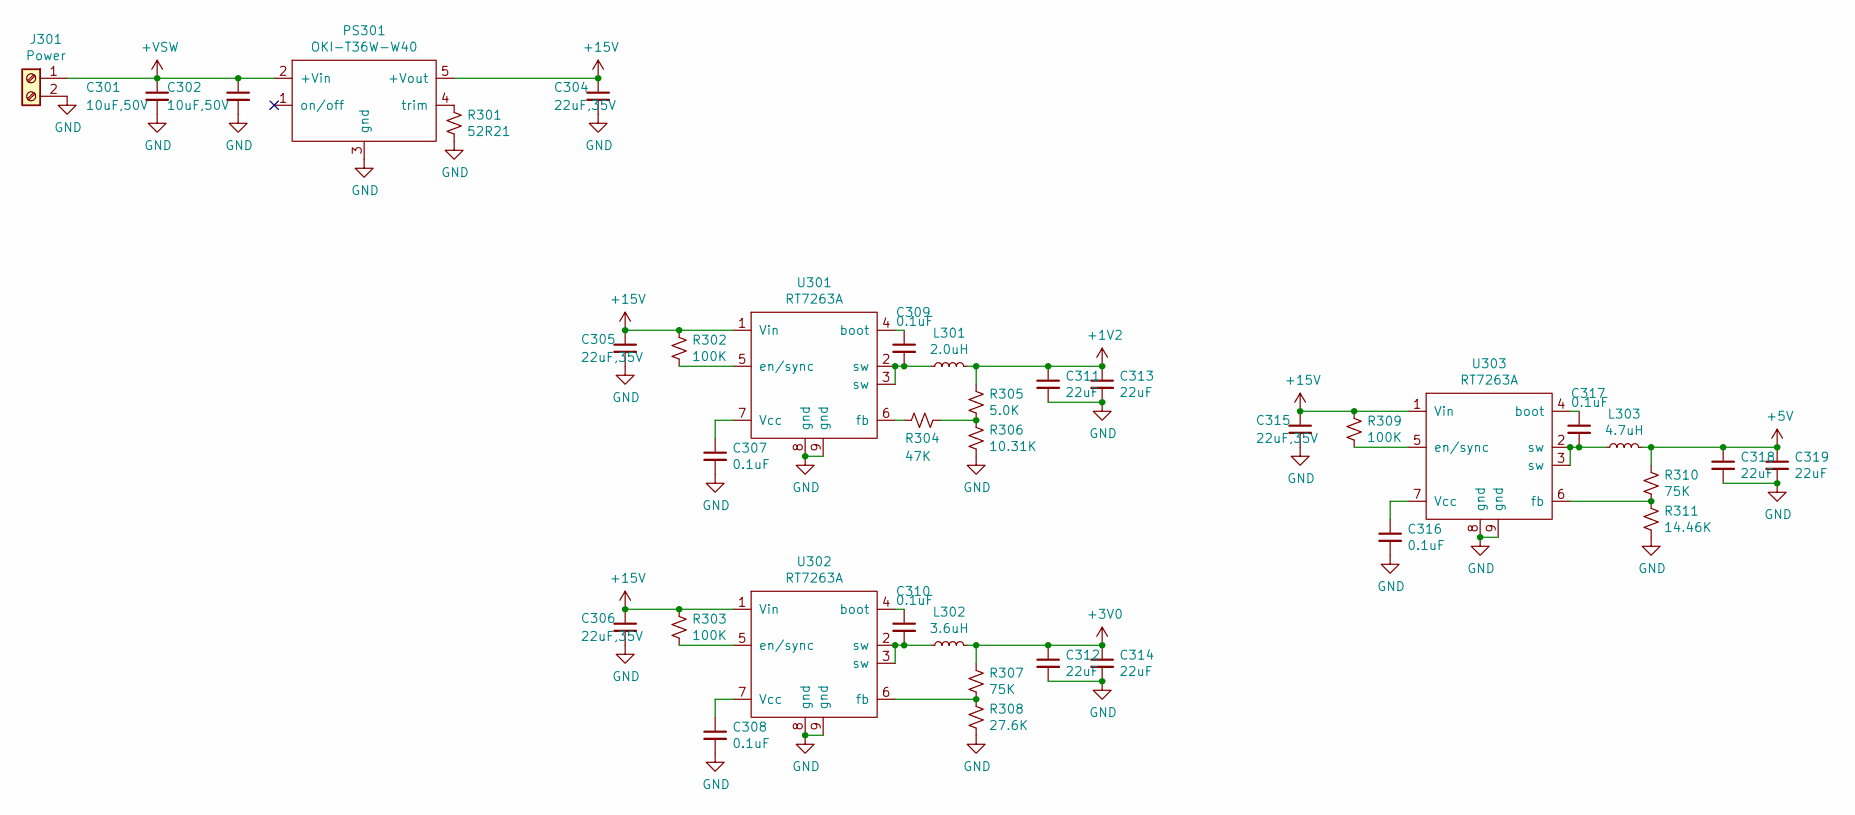
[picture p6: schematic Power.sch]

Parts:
C301, C302: 10uF,50V; R_1210_3225Metric
C304, C305, C306, C315: 22uF,35V; C_1210_3225Metric
C307, C308, C309, C310, C316, C317: 0.1uF; C_0402_1005Metric
C311, C312, C313, C314, C318, C319: 22uF; C_1210_3225Metric
J301: Power; Molex_70555_RA_1x02_P2.54
L301: 2.0uH; NR8040
L302: 3.6uH; NR8040
L303: 4.7uH; NR8040
PS301: OKI-T36W-W40; OKI-T-36W-W40
R301: 52R21; R_0603_1608Metric
R302, R303, R309: 100K; R_0402_1005Metric
R304: 47K; R_0402_1005Metric
R305: 5.0K; R_0402_1005Metric
R306: 10.31K; R_0402_1005Metric
R307, R310: 75K; R_0402_1005Metric
R308: 27.6K; R_0402_1005Metric
R311: 14.46K; R_0402_1005Metric
U301, U302, U303: RT7263A; SOP-EP-8_3.9x4.9mm_P1.27mm

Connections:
+1V2: C311.1, C313.1, L301.2, R305.1; also elsewhere on the board
+3V0: C312.1, C314.1, L302.2, R307.1; also elsewhere on the board
+5V: C318.1, C319.1, L303.2, R310.1; also elsewhere on the board
+15V: C304.1, C305.1, C306.1, C315.1, PS301.5 (+Vout), R302.1, R303.1, R309.1, U301.1 (Vin), U302.1 (Vin), U303.1 (Vin); also elsewhere on the board
+VSW: C301.1, C302.1, J301.1, PS301.2 (+Vin); also elsewhere on the board
GND: C301.2, C302.2, C304.2, C305.2, C306.2, C307.2, C308.2, C311.2, C312.2, C313.2, C314.2, C315.2, C316.2, C318.2, C319.2, J301.2, PS301.3 (gnd), R301.2, R306.2, R308.2, R311.2, U301.8 (gnd), U301.9 (gnd), U302.8 (gnd), U302.9 (gnd), U303.8 (gnd), U303.9 (gnd); also elsewhere on the board
unnamed: C307.1, U301.7 (Vcc)
unnamed: C308.1, U302.7 (Vcc)
unnamed: C309.1, U301.4 (boot)
unnamed: C309.2, L301.1, U301.2 (sw), U301.3 (sw)
unnamed: C310.1, U302.4 (boot)
unnamed: C310.2, L302.1, U302.2 (sw), U302.3 (sw)
unnamed: C316.1, U303.7 (Vcc)
unnamed: C317.1, U303.4 (boot)
unnamed: C317.2, L303.1, U303.2 (sw), U303.3 (sw)
unnamed: PS301.4 (trim), R301.1
unnamed: R302.2, U301.5 (en/sync)
unnamed: R303.2, U302.5 (en/sync)
unnamed: R304.1, R305.2, R306.1
unnamed: R304.2, U301.6 (fb)
unnamed: R307.2, R308.1, U302.6 (fb)
unnamed: R309.2, U303.5 (en/sync)
unnamed: R310.2, R311.1, U303.6 (fb)

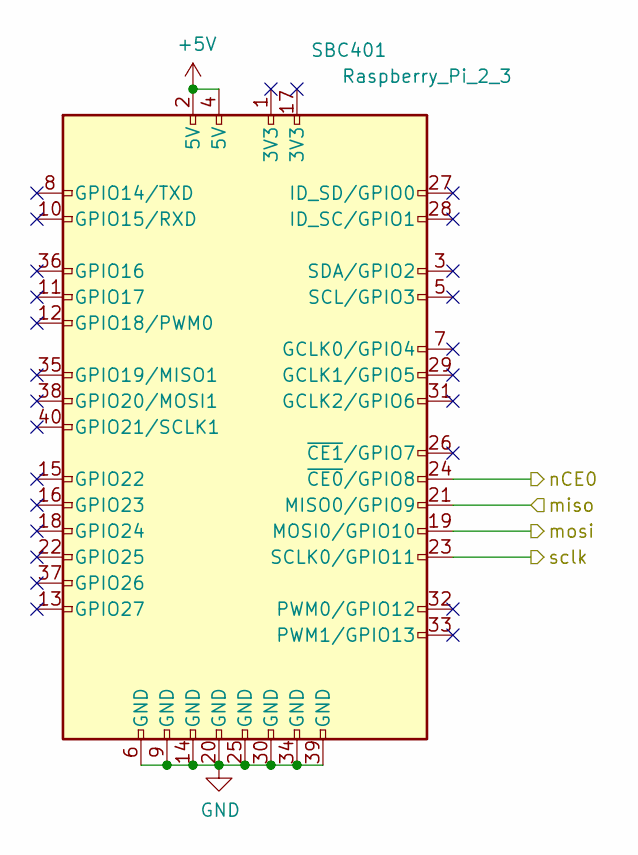
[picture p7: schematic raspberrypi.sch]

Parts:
SBC401: Raspberry_Pi_2_3; Raspberry_Pi_Zero_Socketed_THT_MountingHoles_SMT

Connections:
+5V: SBC401.2 (5V), SBC401.4 (5V); also elsewhere on the board
/Raspberry PI/mosi: SBC401.19 (MOSI0/GPIO10); also elsewhere on the board
/Raspberry PI/nCE0: SBC401.24 (~CE0~/GPIO8); also elsewhere on the board
/Raspberry PI/sclk: SBC401.23 (SCLK0/GPIO11); also elsewhere on the board
/miso: SBC401.21 (MISO0/GPIO9); also elsewhere on the board
GND: SBC401.6 (GND), SBC401.9 (GND), SBC401.14 (GND), SBC401.20 (GND), SBC401.25 (GND), SBC401.30 (GND), SBC401.34 (GND), SBC401.39 (GND); also elsewhere on the board

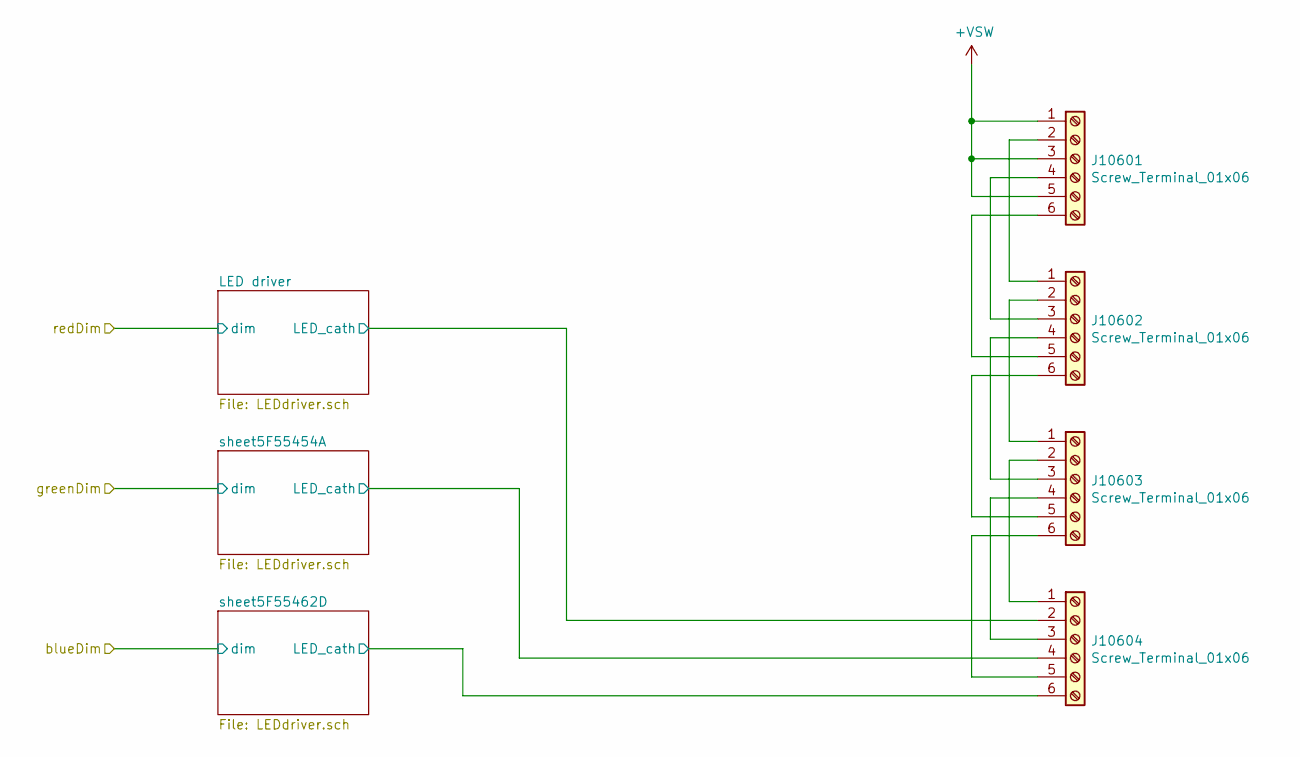
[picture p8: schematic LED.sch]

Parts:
J10601, J10602, J10603, J10604: Screw_Terminal_01x06; Hirose_DF13-06P-1.25DS_1x06_P1.25mm_Horizontal

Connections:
+VSW: J10601.1, J10601.3, J10601.5; also elsewhere on the board
/LED/LED driver/LED_cath: J10604.2; also elsewhere on the board
/LED/sheet5F55454A/LED_cath: J10604.4; also elsewhere on the board
/LED/sheet5F55462D/LED_cath: J10604.6; also elsewhere on the board
unnamed: J10601.2, J10602.1
unnamed: J10601.4, J10602.3
unnamed: J10601.6, J10602.5
unnamed: J10602.2, J10603.1
unnamed: J10602.4, J10603.3
unnamed: J10602.6, J10603.5
unnamed: J10603.2, J10604.1
unnamed: J10603.4, J10604.3
unnamed: J10603.6, J10604.5

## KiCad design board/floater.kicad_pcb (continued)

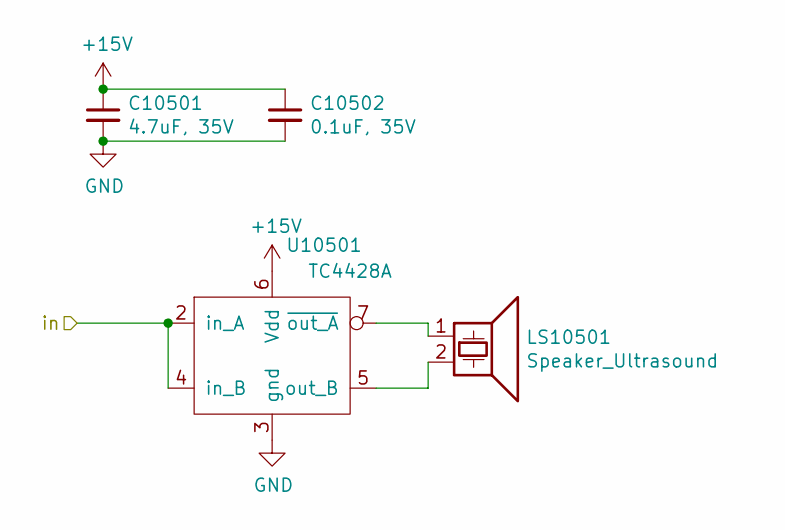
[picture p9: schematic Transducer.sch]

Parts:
C601: 4.7uF, 35V; C_1206_3216Metric
C602: 0.1uF, 35V; C_0805_2012Metric
LS601: Speaker_Ultrasound; MSO-P1040H07T
U601: TC4428A; SO-8_3.9x4.9mm_P1.27mm

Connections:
+15V: C601.1, C602.1, U601.6 (Vdd); also elsewhere on the board
/FPGA2/t40: U601.2 (in_A), U601.4 (in_B); also elsewhere on the board
GND: C601.2, C602.2, U601.3 (gnd); also elsewhere on the board
unnamed: LS601.1, U601.7 (~out_A)
unnamed: LS601.2, U601.5 (out_B)

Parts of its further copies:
C701, C801, C901, C1001, C1101, C1201, C1301, C1401, C1501, C1601, C1701, C1801, C1901, C2001, C2101, C2201, C2301, C2401, C2501, C2601, C2701, C2801, C2901, C3001, C3101, C3201, C3301, C3401, C3501, C3601, C3701, C3801, C3901, C4001, C4101, C4201, C4301, C4401, C4501, C4601, C4701, C4801, C4901, C5001, C5101, C5201, C5301, C5401, C5501, C5601, C5701, C5801, C5901, C6001, C6101, C6201, C6301, C6401, C6501, C6601, C6701, C6801, C6901, C7001, C7101, C7201, C7301, C7401, C7501, C7601, C7701, C7801, C7901, C8001, C8101, C8201, C8301, C8401, C8501, C8601, C8701, C8801, C8901, C9001, C9101, C9201, C9301, C9401, C9501, C9601, C9701, C9801, C9901, C10001, C10101, C10201, C10301, C10401, C10501: 4.7uF, 35V; C_1206_3216Metric
C702, C802, C902, C1002, C1102, C1202, C1302, C1402, C1502, C1602, C1702, C1802, C1902, C2002, C2102, C2202, C2302, C2402, C2502, C2602, C2702, C2802, C2902, C3002, C3102, C3202, C3302, C3402, C3502, C3602, C3702, C3802, C3902, C4002, C4102, C4202, C4302, C4402, C4502, C4602, C4702, C4802, C4902, C5002, C5102, C5202, C5302, C5402, C5502, C5602, C5702, C5802, C5902, C6002, C6102, C6202, C6302, C6402, C6502, C6602, C6702, C6802, C6902, C7002, C7102, C7202, C7302, C7402, C7502, C7602, C7702, C7802, C7902, C8002, C8102, C8202, C8302, C8402, C8502, C8602, C8702, C8802, C8902, C9002, C9102, C9202, C9302, C9402, C9502, C9602, C9702, C9802, C9902, C10002, C10102, C10202, C10302, C10402, C10502: 0.1uF, 35V; C_0805_2012Metric
LS701, LS801, LS901, LS1001, LS1101, LS1201, LS1301, LS1401, LS1501, LS1601, LS1701, LS1801, LS1901, LS2001, LS2101, LS2201, LS2301, LS2401, LS2501, LS2601, LS2701, LS2801, LS2901, LS3001, LS3101, LS3201, LS3301, LS3401, LS3501, LS3601, LS3701, LS3801, LS3901, LS4001, LS4101, LS4201, LS4301, LS4401, LS4501, LS4601, LS4701, LS4801, LS4901, LS5001, LS5101, LS5201, LS5301, LS5401, LS5501, LS5601, LS5701, LS5801, LS5901, LS6001, LS6101, LS6201, LS6301, LS6401, LS6501, LS6601, LS6701, LS6801, LS6901, LS7001, LS7101, LS7201, LS7301, LS7401, LS7501, LS7601, LS7701, LS7801, LS7901, LS8001, LS8101, LS8201, LS8301, LS8401, LS8501, LS8601, LS8701, LS8801, LS8901, LS9001, LS9101, LS9201, LS9301, LS9401, LS9501, LS9601, LS9701, LS9801, LS9901, LS10001, LS10101, LS10201, LS10301, LS10401, LS10501: Speaker_Ultrasound; MSO-P1040H07T
U701, U801, U901, U1001, U1101, U1201, U1301, U1401, U1501, U1601, U1701, U1801, U1901, U2001, U2101, U2201, U2301, U2401, U2501, U2601, U2701, U2801, U2901, U3001, U3101, U3201, U3301, U3401, U3501, U3601, U3701, U3801, U3901, U4001, U4101, U4201, U4301, U4401, U4501, U4601, U4701, U4801, U4901, U5001, U5101, U5201, U5301, U5401, U5501, U5601, U5701, U5801, U5901, U6001, U6101, U6201, U6301, U6401, U6501, U6601, U6701, U6801, U6901, U7001, U7101, U7201, U7301, U7401, U7501, U7601, U7701, U7801, U7901, U8001, U8101, U8201, U8301, U8401, U8501, U8601, U8701, U8801, U8901, U9001, U9101, U9201, U9301, U9401, U9501, U9601, U9701, U9801, U9901, U10001, U10101, U10201, U10301, U10401, U10501: TC4428A; SO-8_3.9x4.9mm_P1.27mm

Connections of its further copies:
+15V: C701.1, C702.1, C801.1, C802.1, C901.1, C902.1, C1001.1, C1002.1, C1101.1, C1102.1, C1201.1, C1202.1, C1301.1, C1302.1, C1401.1, C1402.1, C1501.1, C1502.1, C1601.1, C1602.1, C1701.1, C1702.1, C1801.1, C1802.1, C1901.1, C1902.1, C2001.1, C2002.1, C2101.1, C2102.1, C2201.1, C2202.1, C2301.1, C2302.1, C2401.1, C2402.1, C2501.1, C2502.1, C2601.1, C2602.1, C2701.1, C2702.1, C2801.1, C2802.1, C2901.1, C2902.1, C3001.1, C3002.1, C3101.1, C3102.1, C3201.1, C3202.1, C3301.1, C3302.1, C3401.1, C3402.1, C3501.1, C3502.1, C3601.1, C3602.1, C3701.1, C3702.1, C3801.1, C3802.1, C3901.1, C3902.1, C4001.1, C4002.1, C4101.1, C4102.1, C4201.1, C4202.1, C4301.1, C4302.1, C4401.1, C4402.1, C4501.1, C4502.1, C4601.1, C4602.1, C4701.1, C4702.1, C4801.1, C4802.1, C4901.1, C4902.1, C5001.1, C5002.1, C5101.1, C5102.1, C5201.1, C5202.1, C5301.1, C5302.1, C5401.1, C5402.1, C5501.1, C5502.1, C5601.1, C5602.1, C5701.1, C5702.1, C5801.1, C5802.1, C5901.1, C5902.1, C6001.1, C6002.1, C6101.1, C6102.1, C6201.1, C6202.1, C6301.1, C6302.1, C6401.1, C6402.1, C6501.1, C6502.1, C6601.1, C6602.1, C6701.1, C6702.1, C6801.1, C6802.1, C6901.1, C6902.1, C7001.1, C7002.1, C7101.1, C7102.1, C7201.1, C7202.1, C7301.1, C7302.1, C7401.1, C7402.1, C7501.1, C7502.1, C7601.1, C7602.1, C7701.1, C7702.1, C7801.1, C7802.1, C7901.1, C7902.1, C8001.1, C8002.1, C8101.1, C8102.1, C8201.1, C8202.1, C8301.1, C8302.1, C8401.1, C8402.1, C8501.1, C8502.1, C8601.1, C8602.1, C8701.1, C8702.1, C8801.1, C8802.1, C8901.1, C8902.1, C9001.1, C9002.1, C9101.1, C9102.1, C9201.1, C9202.1, C9301.1, C9302.1, C9401.1, C9402.1, C9501.1, C9502.1, C9601.1, C9602.1, C9701.1, C9702.1, C9801.1, C9802.1, C9901.1, C9902.1, C10001.1, C10002.1, C10101.1, C10102.1, C10201.1, C10202.1, C10301.1, C10302.1, C10401.1, C10402.1, C10501.1, C10502.1, U701.6 (Vdd), U801.6 (Vdd), U901.6 (Vdd), U1001.6 (Vdd), U1101.6 (Vdd), U1201.6 (Vdd), U1301.6 (Vdd), U1401.6 (Vdd), U1501.6 (Vdd), U1601.6 (Vdd), U1701.6 (Vdd), U1801.6 (Vdd), U1901.6 (Vdd), U2001.6 (Vdd), U2101.6 (Vdd), U2201.6 (Vdd), U2301.6 (Vdd), U2401.6 (Vdd), U2501.6 (Vdd), U2601.6 (Vdd), U2701.6 (Vdd), U2801.6 (Vdd), U2901.6 (Vdd), U3001.6 (Vdd), U3101.6 (Vdd), U3201.6 (Vdd), U3301.6 (Vdd), U3401.6 (Vdd), U3501.6 (Vdd), U3601.6 (Vdd), U3701.6 (Vdd), U3801.6 (Vdd), U3901.6 (Vdd), U4001.6 (Vdd), U4101.6 (Vdd), U4201.6 (Vdd), U4301.6 (Vdd), U4401.6 (Vdd), U4501.6 (Vdd), U4601.6 (Vdd), U4701.6 (Vdd), U4801.6 (Vdd), U4901.6 (Vdd), U5001.6 (Vdd), U5101.6 (Vdd), U5201.6 (Vdd), U5301.6 (Vdd), U5401.6 (Vdd), U5501.6 (Vdd), U5601.6 (Vdd), U5701.6 (Vdd), U5801.6 (Vdd), U5901.6 (Vdd), U6001.6 (Vdd), U6101.6 (Vdd), U6201.6 (Vdd), U6301.6 (Vdd), U6401.6 (Vdd), U6501.6 (Vdd), U6601.6 (Vdd), U6701.6 (Vdd), U6801.6 (Vdd), U6901.6 (Vdd), U7001.6 (Vdd), U7101.6 (Vdd), U7201.6 (Vdd), U7301.6 (Vdd), U7401.6 (Vdd), U7501.6 (Vdd), U7601.6 (Vdd), U7701.6 (Vdd), U7801.6 (Vdd), U7901.6 (Vdd), U8001.6 (Vdd), U8101.6 (Vdd), U8201.6 (Vdd), U8301.6 (Vdd), U8401.6 (Vdd), U8501.6 (Vdd), U8601.6 (Vdd), U8701.6 (Vdd), U8801.6 (Vdd), U8901.6 (Vdd), U9001.6 (Vdd), U9101.6 (Vdd), U9201.6 (Vdd), U9301.6 (Vdd), U9401.6 (Vdd), U9501.6 (Vdd), U9601.6 (Vdd), U9701.6 (Vdd), U9801.6 (Vdd), U9901.6 (Vdd), U10001.6 (Vdd), U10101.6 (Vdd), U10201.6 (Vdd), U10301.6 (Vdd), U10401.6 (Vdd), U10501.6 (Vdd); also elsewhere on the board
/FPGA2/t0: U4601.2 (in_A), U4601.4 (in_B); also elsewhere on the board
/FPGA2/t1: U4701.2 (in_A), U4701.4 (in_B); also elsewhere on the board
/FPGA2/t2: U4801.2 (in_A), U4801.4 (in_B); also elsewhere on the board
/FPGA2/t3: U4901.2 (in_A), U4901.4 (in_B); also elsewhere on the board
/FPGA2/t4: U5001.2 (in_A), U5001.4 (in_B); also elsewhere on the board
/FPGA2/t5: U5101.2 (in_A), U5101.4 (in_B); also elsewhere on the board
/FPGA2/t6: U5201.2 (in_A), U5201.4 (in_B); also elsewhere on the board
/FPGA2/t7: U5301.2 (in_A), U5301.4 (in_B); also elsewhere on the board
/FPGA2/t8: U5401.2 (in_A), U5401.4 (in_B); also elsewhere on the board
/FPGA2/t9: U5501.2 (in_A), U5501.4 (in_B); also elsewhere on the board
/FPGA2/t10: U3601.2 (in_A), U3601.4 (in_B); also elsewhere on the board
/FPGA2/t11: U3701.2 (in_A), U3701.4 (in_B); also elsewhere on the board
/FPGA2/t12: U3801.2 (in_A), U3801.4 (in_B); also elsewhere on the board
/FPGA2/t13: U3901.2 (in_A), U3901.4 (in_B); also elsewhere on the board
/FPGA2/t14: U4001.2 (in_A), U4001.4 (in_B); also elsewhere on the board
/FPGA2/t15: U4101.2 (in_A), U4101.4 (in_B); also elsewhere on the board
/FPGA2/t16: U4201.2 (in_A), U4201.4 (in_B); also elsewhere on the board
/FPGA2/t17: U4301.2 (in_A), U4301.4 (in_B); also elsewhere on the board
/FPGA2/t18: U4401.2 (in_A), U4401.4 (in_B); also elsewhere on the board
/FPGA2/t19: U4501.2 (in_A), U4501.4 (in_B); also elsewhere on the board
/FPGA2/t20: U2601.2 (in_A), U2601.4 (in_B); also elsewhere on the board
/FPGA2/t21: U2701.2 (in_A), U2701.4 (in_B); also elsewhere on the board
/FPGA2/t22: U2801.2 (in_A), U2801.4 (in_B); also elsewhere on the board
/FPGA2/t23: U2901.2 (in_A), U2901.4 (in_B); also elsewhere on the board
/FPGA2/t24: U3001.2 (in_A), U3001.4 (in_B); also elsewhere on the board
/FPGA2/t25: U3101.2 (in_A), U3101.4 (in_B); also elsewhere on the board
/FPGA2/t26: U3201.2 (in_A), U3201.4 (in_B); also elsewhere on the board
/FPGA2/t27: U3301.2 (in_A), U3301.4 (in_B); also elsewhere on the board
/FPGA2/t28: U3401.2 (in_A), U3401.4 (in_B); also elsewhere on the board
/FPGA2/t29: U3501.2 (in_A), U3501.4 (in_B); also elsewhere on the board
/FPGA2/t30: U1601.2 (in_A), U1601.4 (in_B); also elsewhere on the board
/FPGA2/t31: U1701.2 (in_A), U1701.4 (in_B); also elsewhere on the board
/FPGA2/t32: U1801.2 (in_A), U1801.4 (in_B); also elsewhere on the board
/FPGA2/t33: U1901.2 (in_A), U1901.4 (in_B); also elsewhere on the board
/FPGA2/t34: U2001.2 (in_A), U2001.4 (in_B); also elsewhere on the board
/FPGA2/t35: U2101.2 (in_A), U2101.4 (in_B); also elsewhere on the board
/FPGA2/t36: U2201.2 (in_A), U2201.4 (in_B); also elsewhere on the board
/FPGA2/t37: U2301.2 (in_A), U2301.4 (in_B); also elsewhere on the board
/FPGA2/t38: U2401.2 (in_A), U2401.4 (in_B); also elsewhere on the board
/FPGA2/t39: U2501.2 (in_A), U2501.4 (in_B); also elsewhere on the board
/FPGA2/t41: U701.2 (in_A), U701.4 (in_B); also elsewhere on the board
/FPGA2/t42: U801.2 (in_A), U801.4 (in_B); also elsewhere on the board
/FPGA2/t43: U901.2 (in_A), U901.4 (in_B); also elsewhere on the board
/FPGA2/t44: U1001.2 (in_A), U1001.4 (in_B); also elsewhere on the board
/FPGA2/t45: U1101.2 (in_A), U1101.4 (in_B); also elsewhere on the board
/FPGA2/t46: U1201.2 (in_A), U1201.4 (in_B); also elsewhere on the board
/FPGA2/t47: U1301.2 (in_A), U1301.4 (in_B); also elsewhere on the board
/FPGA2/t48: U1401.2 (in_A), U1401.4 (in_B); also elsewhere on the board
/FPGA2/t49: U1501.2 (in_A), U1501.4 (in_B); also elsewhere on the board
/Transducers/s0: U9601.2 (in_A), U9601.4 (in_B); also elsewhere on the board
/Transducers/s1: U9701.2 (in_A), U9701.4 (in_B); also elsewhere on the board
/Transducers/s2: U9801.2 (in_A), U9801.4 (in_B); also elsewhere on the board
/Transducers/s3: U9901.2 (in_A), U9901.4 (in_B); also elsewhere on the board
/Transducers/s4: U10001.2 (in_A), U10001.4 (in_B); also elsewhere on the board
/Transducers/s5: U10101.2 (in_A), U10101.4 (in_B); also elsewhere on the board
/Transducers/s6: U10201.2 (in_A), U10201.4 (in_B); also elsewhere on the board
/Transducers/s7: U10301.2 (in_A), U10301.4 (in_B); also elsewhere on the board
/Transducers/s8: U10401.2 (in_A), U10401.4 (in_B); also elsewhere on the board
/Transducers/s9: U10501.2 (in_A), U10501.4 (in_B); also elsewhere on the board
/Transducers/s10: U8601.2 (in_A), U8601.4 (in_B); also elsewhere on the board
/Transducers/s11: U8701.2 (in_A), U8701.4 (in_B); also elsewhere on the board
/Transducers/s12: U8801.2 (in_A), U8801.4 (in_B); also elsewhere on the board
/Transducers/s13: U8901.2 (in_A), U8901.4 (in_B); also elsewhere on the board
/Transducers/s14: U9001.2 (in_A), U9001.4 (in_B); also elsewhere on the board
/Transducers/s15: U9101.2 (in_A), U9101.4 (in_B); also elsewhere on the board
/Transducers/s16: U9201.2 (in_A), U9201.4 (in_B); also elsewhere on the board
/Transducers/s17: U9301.2 (in_A), U9301.4 (in_B); also elsewhere on the board
/Transducers/s18: U9401.2 (in_A), U9401.4 (in_B); also elsewhere on the board
/Transducers/s19: U9501.2 (in_A), U9501.4 (in_B); also elsewhere on the board
/Transducers/s20: U7601.2 (in_A), U7601.4 (in_B); also elsewhere on the board
/Transducers/s21: U7701.2 (in_A), U7701.4 (in_B); also elsewhere on the board
/Transducers/s22: U7801.2 (in_A), U7801.4 (in_B); also elsewhere on the board
/Transducers/s23: U7901.2 (in_A), U7901.4 (in_B); also elsewhere on the board
/Transducers/s24: U8001.2 (in_A), U8001.4 (in_B); also elsewhere on the board
/Transducers/s25: U8101.2 (in_A), U8101.4 (in_B); also elsewhere on the board
/Transducers/s26: U8201.2 (in_A), U8201.4 (in_B); also elsewhere on the board
/Transducers/s27: U8301.2 (in_A), U8301.4 (in_B); also elsewhere on the board
/Transducers/s28: U8401.2 (in_A), U8401.4 (in_B); also elsewhere on the board
/Transducers/s29: U8501.2 (in_A), U8501.4 (in_B); also elsewhere on the board
/Transducers/s30: U6601.2 (in_A), U6601.4 (in_B); also elsewhere on the board
/Transducers/s31: U6701.2 (in_A), U6701.4 (in_B); also elsewhere on the board
/Transducers/s32: U6801.2 (in_A), U6801.4 (in_B); also elsewhere on the board
/Transducers/s33: U6901.2 (in_A), U6901.4 (in_B); also elsewhere on the board
/Transducers/s34: U7001.2 (in_A), U7001.4 (in_B); also elsewhere on the board
/Transducers/s35: U7101.2 (in_A), U7101.4 (in_B); also elsewhere on the board
/Transducers/s36: U7201.2 (in_A), U7201.4 (in_B); also elsewhere on the board
/Transducers/s37: U7301.2 (in_A), U7301.4 (in_B); also elsewhere on the board
/Transducers/s38: U7401.2 (in_A), U7401.4 (in_B); also elsewhere on the board
/Transducers/s39: U7501.2 (in_A), U7501.4 (in_B); also elsewhere on the board
/Transducers/s40: U5601.2 (in_A), U5601.4 (in_B); also elsewhere on the board
/Transducers/s41: U5701.2 (in_A), U5701.4 (in_B); also elsewhere on the board
/Transducers/s42: U5801.2 (in_A), U5801.4 (in_B); also elsewhere on the board
/Transducers/s43: U5901.2 (in_A), U5901.4 (in_B); also elsewhere on the board
/Transducers/s44: U6001.2 (in_A), U6001.4 (in_B); also elsewhere on the board
/Transducers/s45: U6101.2 (in_A), U6101.4 (in_B); also elsewhere on the board
/Transducers/s46: U6201.2 (in_A), U6201.4 (in_B); also elsewhere on the board
/Transducers/s47: U6301.2 (in_A), U6301.4 (in_B); also elsewhere on the board
/Transducers/s48: U6401.2 (in_A), U6401.4 (in_B); also elsewhere on the board
/Transducers/s49: U6501.2 (in_A), U6501.4 (in_B); also elsewhere on the board
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

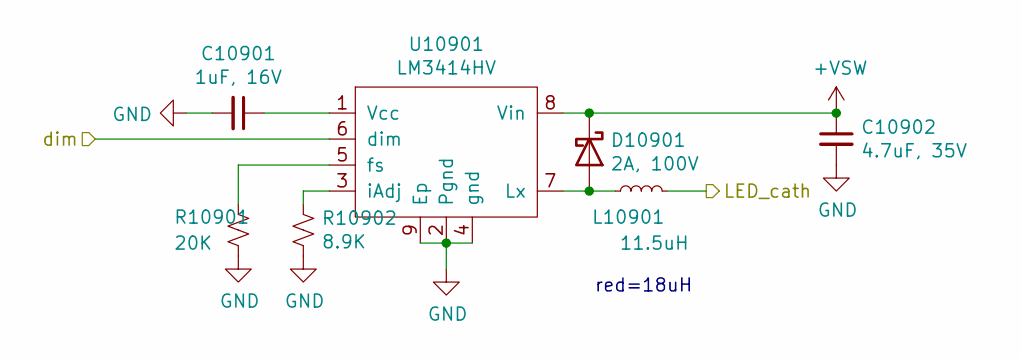
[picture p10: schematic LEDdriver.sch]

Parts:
C10701: 1uF, 16V; C_0805_2012Metric
C10702: 4.7uF, 35V; C_1206_3216Metric
D10701: 2A, 100V; DO-220A
L10701: 11.5uH; SRR6038
R10701: 20K; R_0402_1005Metric
R10702: 8.9K; R_0402_1005Metric
U10701: LM3414HV; SOIC-8-1EP_3.9x4.9mm_P1.27mm_EP2.35x2.35mm

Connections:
+VSW: C10702.1, D10701.1 (K), U10701.8 (Vin); also elsewhere on the board
/LED/LED driver/LED_cath: L10701.2; also elsewhere on the board
/redDim: U10701.6 (dim); also elsewhere on the board
GND: C10701.2, C10702.2, R10701.1, R10702.2, U10701.2 (Pgnd), U10701.4 (gnd), U10701.9 (Ep); also elsewhere on the board
unnamed: C10701.1, U10701.1 (Vcc)
unnamed: D10701.2 (A), L10701.1, U10701.7 (Lx)
unnamed: R10701.2, U10701.5 (fs)
unnamed: R10702.1, U10701.3 (iAdj)

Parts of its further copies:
C10801, C10901: 1uF, 16V; C_0805_2012Metric
C10802, C10902: 4.7uF, 35V; C_1206_3216Metric
D10801, D10901: 2A, 100V; DO-220A
L10801, L10901: 11.5uH; SRR6038
R10801, R10901: 20K; R_0402_1005Metric
R10802, R10902: 8.9K; R_0402_1005Metric
U10801, U10901: LM3414HV; SOIC-8-1EP_3.9x4.9mm_P1.27mm_EP2.35x2.35mm

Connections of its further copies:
+VSW: C10802.1, C10902.1, D10801.1 (K), D10901.1 (K), U10801.8 (Vin), U10901.8 (Vin); also elsewhere on the board
/LED/sheet5F55454A/LED_cath: L10801.2; also elsewhere on the board
/LED/sheet5F55462D/LED_cath: L10901.2; also elsewhere on the board
/blueDim: U10901.6 (dim); also elsewhere on the board
/greenDim: U10801.6 (dim); also elsewhere on the board
GND: C10801.2, C10802.2, C10901.2, C10902.2, R10801.1, R10802.2, R10901.1, R10902.2, U10801.2 (Pgnd), U10801.4 (gnd), U10801.9 (Ep), U10901.2 (Pgnd), U10901.4 (gnd), U10901.9 (Ep); also elsewhere on the board
unnamed: C10801.1, U10801.1 (Vcc)
unnamed: C10901.1, U10901.1 (Vcc)
unnamed: D10801.2 (A), L10801.1, U10801.7 (Lx)
unnamed: D10901.2 (A), L10901.1, U10901.7 (Lx)
unnamed: R10801.2, U10801.5 (fs)
unnamed: R10802.1, U10801.3 (iAdj)
unnamed: R10901.2, U10901.5 (fs)
unnamed: R10902.1, U10901.3 (iAdj)

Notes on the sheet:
red=18uH

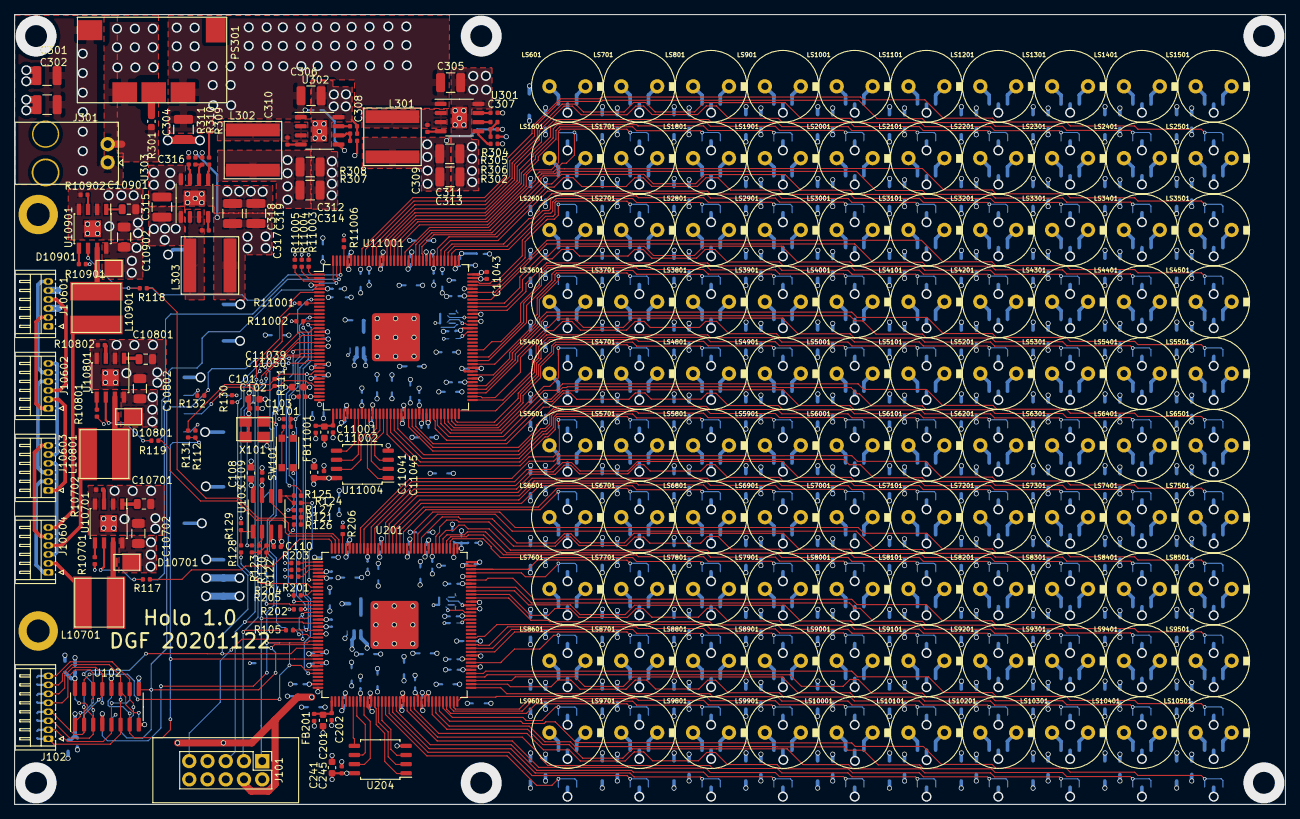
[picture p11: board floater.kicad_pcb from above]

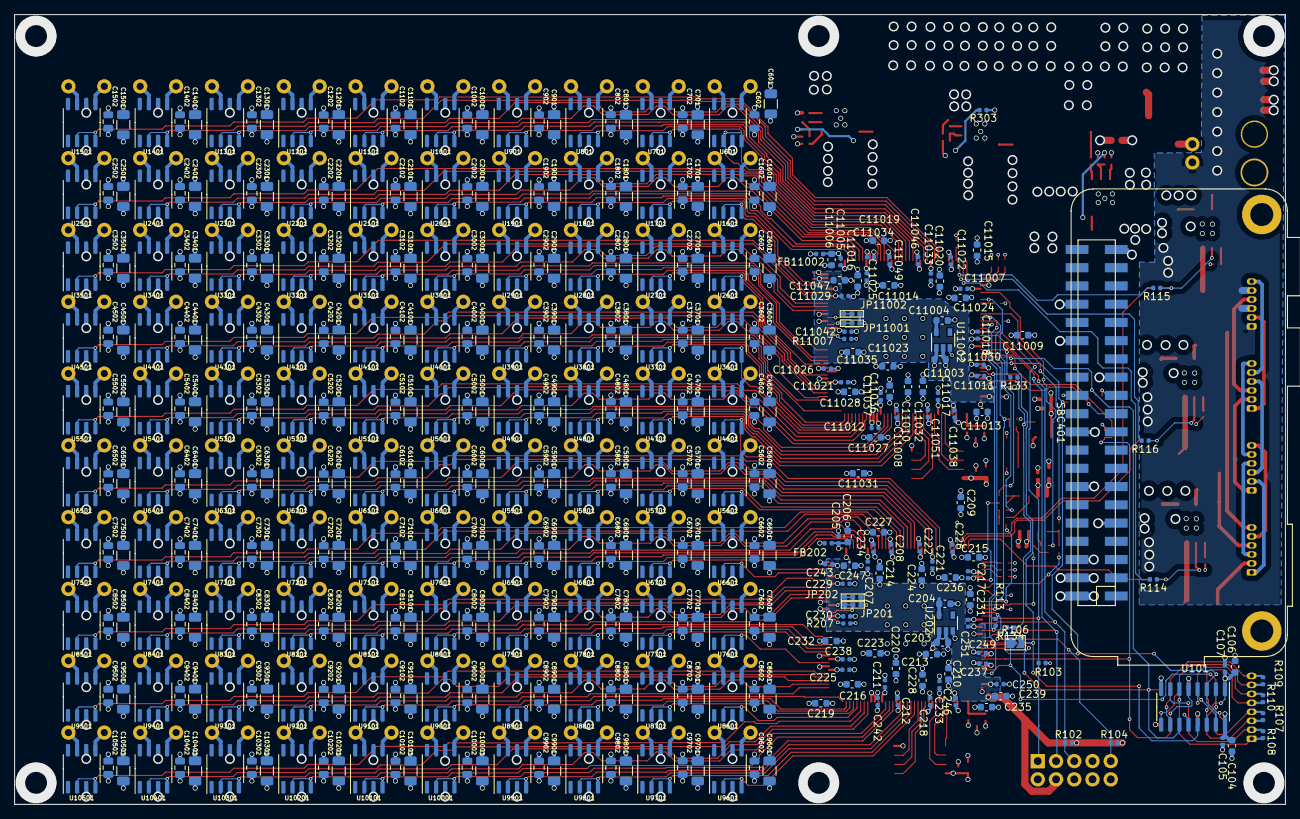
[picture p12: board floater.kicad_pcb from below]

Board: 4 copper layers, 177.0 x 110.0 mm, 638 parts (416 on the bottom side), 432 nets.

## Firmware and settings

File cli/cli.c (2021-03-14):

#include <unistd.h> 
#include <stdio.h> 
#include <sys/socket.h> 
#include <stdlib.h> 
#include <netinet/in.h> 
#include <string.h> 
#include <getopt.h>
#include <fcntl.h>
#include <sys/ioctl.h>
#include <linux/types.h>
#include <linux/spi/spidev.h>
#include <termios.h>
#include <unistd.h>
#include <math.h>


#define BUF_SIZE_BYTES (17)
#define INC 1.0f
#define MOVE_INC 0.1f

#define fabs(x) ((x>0)?x:-x)

static void pabort(const char *s)
{
	perror(s);
	abort();
}

int getch(void) {
    struct termios oldattr, newattr;
    int ch;
    tcgetattr( STDIN_FILENO, &oldattr );
    newattr = oldattr;
    newattr.c_lflag &= ~( ICANON | ECHO );
    tcsetattr( STDIN_FILENO, TCSANOW, &newattr );
    ch = getchar();
    tcsetattr( STDIN_FILENO, TCSANOW, &oldattr );
    return ch;
}

int _kbhit(void)
{
  struct termios oldt, newt;
  int ch;
  int oldf;
 
  tcgetattr(STDIN_FILENO, &oldt);
  newt = oldt;
  newt.c_lflag &= ~(ICANON | ECHO);
  tcsetattr(STDIN_FILENO, TCSANOW, &newt);
  oldf = fcntl(STDIN_FILENO, F_GETFL, 0);
  fcntl(STDIN_FILENO, F_SETFL, oldf | O_NONBLOCK);
 
  ch = getchar();
 
  tcsetattr(STDIN_FILENO, TCSANOW, &oldt);
  fcntl(STDIN_FILENO, F_SETFL, oldf);
 
  if(ch != EOF)
  {
    ungetc(ch, stdin);
    return 1;
  }
 
  return 0;
}

#define FLY_RADIUS 20

#define HOME_X 0
#define HOME_Y 0
#define HOME_Z 0

#define SCALE 10	//mm to 0.1mm units

static const char *device = "/dev/spidev0.0";
static const uint8_t mode = 0;
static const uint8_t bits = 8;
static const uint32_t spiSpeed = 500000;
static const uint16_t delay = 0;
static int spiFD;
int16_t spiTx[(BUF_SIZE_BYTES+1)/2];
int16_t spiRx[(BUF_SIZE_BYTES+1)/2];
float xPos = 0.0f, yPos = HOME_Y, zPos= HOME_Z;
typedef uint32_t bool;
#define true 1
#define false 0

float BoardDistance = 85.22;
const float freq = 40000;
//float speed = 1500;	//mm/s
//float acc = 1.5;		//mm/s^2
float speed = 1250;	//mm/s
float acc = 1.5;	
uint16_t timeFactor =0;

float cenPos[3];
float cenRot[3];
float cenScale[3];

#define D2R(x) (x/180.0*M_PI)

int8_t norm(float x)
{
	return (int8_t)(x * 127);
}

void multiplyMatrix(float* a, float* b, float* r)
{
	float c[16];
	memset(c, 0 , 16 * sizeof(float));
	for (int i = 0; i < 4; ++i) {
      for (int j = 0; j < 4; ++j) {
         for (int k = 0; k < 4; ++k) {
            c[i*4+j] += a[i*4 + k] * b[k*4 + j];
         }
      }
   }

   memcpy(r, c, 16*sizeof(float));
}

void printMatrix(float* a)
{
	for (int i = 0; i < 4; ++i) {
      for (int j = 0; j < 4; ++j) {
		  printf("%f\t", a[i*4+j]);
	  }
	  printf("\n");
	}
}

void transfer(int len)
{
	int ret;

	struct spi_ioc_transfer tr = {
		.tx_buf = (unsigned long)spiTx+1,
		.rx_buf = (unsigned long)spiRx+1,
		.len = len+1,
		.delay_usecs = delay,
		.speed_hz = spiSpeed,
		.bits_per_word = bits,
	};

	ret = ioctl(spiFD, SPI_IOC_MESSAGE(1), &tr);
	if (ret < 1)
		pabort("can't send spi message");

	/*uint8_t *ptr = (uint8_t*)spiTx + 1;
	for(int i=0; i<len+1;i++)
		printf("%.2X, ", *ptr++);

	printf("\n");*/
}

void initSPI()
{
	int ret;

	spiFD = open(device, O_RDWR);
	if (spiFD < 0)
		pabort("can't open device");

	ret = ioctl(spiFD, SPI_IOC_WR_MODE, &mode);
	if (ret == -1)
		pabort("can't set spi mode");

	ret = ioctl(spiFD, SPI_IOC_WR_BITS_PER_WORD, &bits);
	if (ret == -1)
		pabort("can't set bits per word");

	ret = ioctl(spiFD, SPI_IOC_WR_MAX_SPEED_HZ, &spiSpeed);
	if (ret == -1)
		pabort("can't set max speed hz");


	printf("spi mode: %d\n", mode);
	printf("bits per word: %d\n", bits);
	printf("max speed: %d Hz (%d KHz)\n", spiSpeed, spiSpeed/1000);
}

void closeSPI()
{
	close(spiFD);
}

void printPos()
{
	printf("%.1f, %.1f, %.1f\n", xPos, yPos, zPos);
}

void sendRawMove(uint16_t r0, uint16_t r1, uint16_t r2, uint16_t r3)
{
	spiTx[0]=3<<9;
	spiTx[1]=r0;
	spiTx[2]=r1;
	spiTx[3]=r2;
	spiTx[4]=r3;

	transfer(8);
}

void sendmove(float x, float y, float z)
{
	spiTx[0]=3<<9;
	spiTx[1]=x*SCALE;
	spiTx[2]=y*SCALE;
	spiTx[3]=z*SCALE;
	spiTx[4]=0;
	
	xPos=x;
	yPos=y;
	zPos=z;
	
	//printPos();
	
	transfer(8);
}

void sendmoveCol(float x, float y, float z, float r, float g, float b)
{
	spiTx[0]=3<<9;
	spiTx[1]=x*SCALE;
	spiTx[2]=y*SCALE;
	spiTx[3]=z*SCALE;
	uint8_t red = 3.0f * r; 
	uint8_t green = 7.0f * g;
	uint8_t blue = 3.0f *b;
	spiTx[4]= blue << 5 | green << 2 | red ;
	//printf("%0.2X\n", spiTx[4]);
	xPos=x;
	yPos=y;
	zPos=z;
	
	//printPos();
	
	transfer(8);
}


void pauseFifoProcessing(bool b)
{
	spiTx[0]=7<<9;
	spiTx[1]=!b ? 0xffff : 0x0000;
	spiTx[2]=0;
	spiTx[3]=0;
	spiTx[4]=0;
	
	transfer(8);
}

void move(float x, float y, float z)
{
	pauseFifoProcessing(true);
	sendRawMove(0, 1, 0, 0);
	sendmove(x, y, z);
	pauseFifoProcessing(false);
}

void moveCol(float x, float y, float z, float r, float g, float b)
{
	pauseFifoProcessing(true);
	sendRawMove(0, 1, 0, 0);
	sendmoveCol(x, y, z, r, g, b);
	pauseFifoProcessing(false);
}

void printSpeed()
{
	//printf("%.0f mm/s\n", speed);
	printf("%d\n", speed);
}

void sendMatrix()
{
	int8_t coeff[9];

	float angles[]={D2R(cenRot[0]), D2R(cenRot[1]), D2R(cenRot[2])};

	float Rz[] = {	cosf(angles[2]), 	-sinf(angles[2]), 	0,			0, 
					sinf(angles[2]), 	cosf(angles[2]), 	0, 			0,
					0, 					0, 					1,			0,
					0,					0,					0,			1
				};

	float Ry[] = {	cosf(angles[1]), 	0,					sinf(angles[1]), 		0,			
					0 ,					1,					0,						0,
					-sinf(angles[1]),	0,					cosf(angles[1]),		0,			
					0,					0,					0,						1	
				};

	float Rx[] = {	1 ,					0,					0,					0,
					0,					cosf(angles[0]),	-sinf(angles[0]),	0,
					0,					sinf(angles[0]), 	cosf(angles[0]), 	0,			
					0,					0,					0,					1
				};
	
	float Scale[] = {	cenScale[0],	0,				0,				0,
						0,				cenScale[1],	0,				0,
						0,				0,				cenScale[2],	0,
						0,				0,				0,				1
	};

	float result[16];

	multiplyMatrix(Scale, Rx, result);
	multiplyMatrix(Ry, result, result);
	multiplyMatrix(Rz, result, result);

	coeff[0]=norm(result[0]);
	coeff[1]=norm(result[1]);
	coeff[2]=norm(result[2]);

	coeff[3]=norm(result[4]);
	coeff[4]=norm(result[5]);
	coeff[5]=norm(result[6]);

	coeff[6]=norm(result[8]);
	coeff[7]=norm(result[9]);
	coeff[8]=norm(result[10]);
	
	/* for (int i = 0; i < 3; ++i) {
      for (int j = 0; j < 3; ++j) {
		  printf("%d\t", coeff[i*3+j]);
	  }
	  printf("\n");
	}*/

	spiTx[0]=10<<9;
	spiTx[1]=((uint8_t)coeff[1] << 8) | (uint8_t)coeff[0];
	spiTx[2]=((uint8_t)coeff[3] << 8) | (uint8_t)coeff[2];
	spiTx[3]=((uint8_t)coeff[5] << 8) | (uint8_t)coeff[4];
	spiTx[4]=((uint8_t)coeff[7] << 8) | (uint8_t)coeff[6];
	spiTx[5]=(uint8_t)coeff[8];
	spiTx[6]=cenPos[0]*SCALE;
	spiTx[7]=cenPos[1]*SCALE;
	spiTx[8]=cenPos[2]*SCALE;
	transfer(16);

	usleep(1000);
  
}

int lineTo(int compIdx, float d, float r, float g, float b)
{
	float maxV = speed/freq;
	float maxA = acc/freq;
	
	maxA = d >0 ? maxA : -maxA;
	
	float components[3]={xPos, yPos, zPos};
	
	float v = 0;
	float pos = 0;
	float posStart = components[compIdx];
	
	float accPos =0;
	
	int cnt=0;
	
	bool halfwayReached = false;
	while(1)
	{
		v+=maxA;
		pos+=v;
		components[compIdx] = posStart + pos ;
		
 
		//if(cnt%2)
			sendmoveCol(components[0], components[1], components[2], r, g, b);
		cnt++;
		
		if(fabs(v)>=maxV) 
		{
			v= d >0 ? maxV : -maxV;
			accPos = pos;
			break;
		}
		
		if((d>0 && pos>=d/2) || (d<0 && pos<=d/2))
		{
			//printf("F: %.1f, %.1f, %.1f   %f, %f\n", xPos, yPos, zPos, d, pos);
			halfwayReached = true;
			break;
		}
		//printf("A: %.1f, %.1f, %.1f\n", xPos, yPos, zPos);
	}
	
	if(!halfwayReached)
	{
		if(d>0) {
			for( ; pos<=d-accPos; pos+= v)
			{
				components[compIdx] = posStart + pos ;
			
				//if(cnt%2)
					sendmoveCol(components[0], components[1], components[2], r, g, b);
				//printf("B: %.1f, %.1f, %.1f\n", xPos, yPos, zPos);
				cnt++;
			}
		} else {
			//printf("G: %.1f, %.1f, %.1f   %f, %f, %f, %f\n", xPos, yPos, zPos, d, pos, v, accPos);
			for( ; pos>=d-accPos; pos+= v)
			{
				components[compIdx] = posStart + pos ;
			
				//if(cnt%2)
					sendmoveCol(components[0], components[1], components[2], r, g, b);
				//printf("C: %.1f, %.1f, %.1f\n", xPos, yPos, zPos);
				cnt++;
			}
		}
		
	} 
	
	while(1)
	{
		v-=maxA;
		pos+=v;
		components[compIdx] = posStart + pos ;
		
		//if(cnt%2)
			sendmoveCol(components[0], components[1], components[2], r, g, b);
		//printf("D: %.1f, %.1f, %.1f\n", xPos, yPos, zPos);
		cnt++;
		
		if((d>0 && v<=0) || (d<0 && v>=0)) 
			break;
	}
	
	return cnt;
}

void sendProfile()
{
	pauseFifoProcessing(true);
	int cnt=0;
/*
#define SZ 30
#define NUM 4824
	sendRawMove(NUM+1, NUM, 0, 0);
	cnt+=lineTo(0, -2*SZ, 1, 1, 1);
	cnt+=lineTo(0, 2*SZ, 1, 1, 1);

	sendRawMove(NUM+1, 1, 10000, 0);
	sendmoveCol(SZ,0,0, 1 ,1,1);
*/

#define SZ 20
#define NUM 5840
sendRawMove(0, NUM, 0, 0);
	cnt+=lineTo(2, SZ, 1, 1, 1);
	cnt+=lineTo(1, SZ, 1, 1, 1);
	cnt+=lineTo(2, -SZ, 1, 1, 1);
	cnt+=lineTo(1, -SZ, 1, 1, 1);

/*sendRawMove(0, NUM, 50, 0);
	cnt+=lineTo(2, SZ, 0, 1, 0);
	cnt+=lineTo(1, SZ, 0, 1, 0);
	cnt+=lineTo(2, -SZ, 0, 1, 0);
	cnt+=lineTo(1, -SZ, 0, 1, 0);
*/
/*#define SZ 10
	cnt+=lineTo(2, SZ, 0, 0, 1);
	cnt+=lineTo(1, SZ, 0, 1, 0);
	//cnt+=lineTo(2, -SZ, 0, 0, 1);
	//cnt+=lineTo(1, -SZ, 1, 1, 0);
	cnt+=lineTo(0, SZ, 1,1,0);
	cnt+=lineTo(1, -SZ, 1, 0, 0);
	cnt+=lineTo(2, -SZ, 0, 1, 1);
	cnt+=lineTo(0, -SZ, 1,1,1);
*/
/*	#define SZ 20
	#define LOOP 300
	cnt+=lineTo(2, SZ, 0, 0, 1);
	for(int i=0;i<LOOP;i++)
		sendmoveCol(xPos, yPos, zPos, 1,1,1);
	cnt+=lineTo(1, SZ, 0, 1, 0);
	for(int i=0;i<LOOP;i++)
		sendmoveCol(xPos, yPos, zPos, 1,1,1);
	cnt+=lineTo(1, -SZ, 1, 0, 0);
	for(int i=0;i<LOOP;i++)
		sendmoveCol(xPos, yPos, zPos, 1,1,1);
	cnt+=lineTo(2, -SZ, 0, 1, 1);
	for(int i=0;i<LOOP;i++)
		sendmoveCol(xPos, yPos, zPos, 1,1,1);
	cnt+=LOOP*4;
*/

//circle
/*	#define RADIUS 10
	#define PERIMETER 3500
	sendRawMove(0, PERIMETER, 0, 0);

	float deltaAngle =2*M_PI / PERIMETER;
	float angle = 0.0f;

	float colors[][3] = {
		0,		0,		0.5,
		0,		0.5,	0,
		0.5,	0,		0,
		0,		0,		1,
		0,		1,		0,
		1,		0,		0,
		0,		1,		1,
		1,		0,		1,
		1,		1,		0,
		1,		1,		1,
	};

	for(int i=0;i<PERIMETER;i++)
	{
		float z= RADIUS * cosf(angle) - RADIUS;
		float y= RADIUS * sinf(angle);
		float x=0;

		
		//sendmoveCol(x,y,z, fmod(i, PERIMETER/3), fmod(i, PERIMETER/9), fmod(i, PERIMETER/27));
		sendmoveCol(x,y,z, colors[i/(PERIMETER/10)][0], colors[i/(PERIMETER/10)][1], colors[i/(PERIMETER/10)][2]);
		angle += deltaAngle;
	}
	cnt=PERIMETER;
*/  
//butterfly1
/*	#define RADIUS 3
	#define PERIMETER 1000

	for(int i=0; i<4;i++)
	{
		float wingAngle = D2R(20-20*i);

		if(i<3)
			sendRawMove((2*PERIMETER+1) * (i+1), 2*PERIMETER, 2, 0);
		else
			sendRawMove(0, 2*PERIMETER, 2, 0);
		float deltaAngle =2*M_PI / PERIMETER;
		float angle = 0.0f;
		
		float Ry[] = {	cosf(wingAngle), 	0,					sinf(wingAngle), 		0,			
						0 ,					1,					0,						0,
						-sinf(wingAngle),	0,					cosf(wingAngle),		0,			
						0,					0,					0,						1	
					};

		for(int i=0;i<PERIMETER;i++)
		{
			float z= RADIUS * cosf(angle) - RADIUS;
			float y= RADIUS * sinf(angle);
			float x=0;
		
			float x1 = x*Ry[0] + y*Ry[4] + z*Ry[8];
			float y1 = x*Ry[1] + y*Ry[5] + z*Ry[9];
			float z1 = x*Ry[2] + y*Ry[6] + z*Ry[10];

			sendmoveCol(x1,y1,z1, 1 ,1,1);
			angle += deltaAngle;
		}

		angle = 0.0f;
		for(int i=0;i<PERIMETER;i++)
		{
			float z= RADIUS * cosf(angle) - RADIUS;
			float y= RADIUS * sinf(angle);
			float x=0;

			float x1 = x*Ry[0] + y*Ry[4] + z*Ry[8];
			float y1 = x*Ry[1] + y*Ry[5] + z*Ry[9];
			float z1 = x*Ry[2] + y*Ry[6] + z*Ry[10];

			sendmoveCol(x1,y1,-z1, 1 ,1,1);

			angle += deltaAngle;
		}

		cnt+=2*PERIMETER;
	}
*/


/*#define SZ 40
	cnt+=lineTo(2, SZ, 0.75, 0.75, 0.75);
	cnt+=lineTo(2, -SZ, 0.75, 0.75, 0.75);
*/
	printf("cnt=%d\n",cnt);
	sendMatrix();
	pauseFifoProcessing(false);
}
 
void sendHalfDistance(float halfDistance)
{
	spiTx[0]=0x04<<9;
	spiTx[1]=halfDistance*SCALE;
	spiTx[2]=0;
	spiTx[3]=0;
	spiTx[4]=0;
	transfer(8);
}

void setTimeFactor(uint16_t factor)
{
	spiTx[0]=0x02<<9;
	spiTx[1]=factor;
	spiTx[2]=0x0;
	spiTx[3]=0x0;
	spiTx[4]=0;
	transfer(8);

	timeFactor = factor;
}

void sendRadius(float radius)
{
	radius *=SCALE;
	uint32_t r= radius * radius;
	spiTx[0]=0x06<<9;
	spiTx[1]=r;
	spiTx[2]=r>>16;
	spiTx[3]=0x0;
	spiTx[4]=0;
	transfer(8);
}




void moveCenter(float x, float y, float z)
{
	cenPos[0]=x;
	cenPos[1]=y;
	cenPos[2]=z;

	sendMatrix();

	printf("Center %.1f, %.1f, %.1f\n", x, y, z);
	usleep(1000);
}

void rotate(float x, float y, float z)
{
	cenRot[0]=x;
	cenRot[1]=y;
	cenRot[2]=z;

	sendMatrix();

	printf("Center rotate %.1f, %.1f, %.1f\n", x, y, z);
	usleep(1000);
}

float randf(float max)
{
	return (float)rand()/(float)RAND_MAX * 2*max - max;
}
void runFlyAround()
{
	const float ds = 0.2;  
	float a=0;
	const float da = ds / FLY_RADIUS;
	cenRot[2] = 65;

	while(!_kbhit())
	{
		cenPos[0]=FLY_RADIUS * cosf(a);
		//cenPos[1]+=v[1];
		cenPos[2]=FLY_RADIUS * sinf(a);

		cenRot[1] = -90 + a*180/M_PI;
		sendMatrix();

		usleep(50000);

		a += da;
		if(a> 2*M_PI)
			a-=2*M_PI;

		printf("%f, %f, %f \n",cenPos[0], cenPos[1], cenPos[2]);
	}
}

int main(int argc, char const *argv[]) 
{ 
	FILE *fp;
	
	float inc;
	float a;
	float Radius;

	float cenX=FLY_RADIUS;
	float cenY=0;
	float cenZ=0;
	float rotX=0;
	float rotY=0;
	float rotZ=0;

	float scale = 1.0f;
	cenScale[0] = scale;
	cenScale[1] = scale;
	cenScale[2] = scale;

    initSPI();
	pauseFifoProcessing(true);
	
	
	sscanf(argv[1],"%f", &BoardDistance);
	sscanf(argv[2],"%f", &Radius);
	
	sendHalfDistance(BoardDistance/2);
	setTimeFactor(2);
	sendRadius(Radius);
	
	printf("listening\n");
	int cnt =0;
	
	bool done = false;
	while(!done)
	{
		int ch = getch();
		
		switch(ch) {
			case 'H':
				pauseFifoProcessing(true);
				sendRawMove(0, 1, 0, 0);
				sendmoveCol(HOME_X, HOME_Y, HOME_Z,1.0f, 1.0f, 1.0f);
				pauseFifoProcessing(false);
				break;
			case 'h':
				move(HOME_X, HOME_Y, HOME_Z);
				cenX=0;//FLY_RADIUS;
				cenY=0;
				cenZ=0;
				cenScale[0] = 1.0f;
				cenScale[1] = 1.0f;
				cenScale[2] = 1.0f;
				cenPos[0] = 0;//FLY_RADIUS;
				cenPos[1] = 0.0f;
				cenPos[2] = 0.0f;
				cenRot[0] = 0.0f;
				cenRot[1] = 0.0f;
				cenRot[2] = 0.0f;
				rotX=0;
				rotY=0;
				rotZ=0;
				sendMatrix();
				printPos();
				break;
			case 'z':
				zPos-=INC;
				printPos();
				moveCol(xPos,yPos,zPos, 1.0f, 1.0f, 1.0f);
				break;
			case 'a':
				zPos+=INC;
				printPos();
				moveCol(xPos,yPos,zPos, 1.0f, 1.0f, 1.0f);
				break;
			case 'x':
				xPos-=INC;
				printPos();
				moveCol(xPos,yPos,zPos, 1.0f, 1.0f, 1.0f);
				break;
			case 's':
				xPos+=INC;
				printPos();
				moveCol(xPos,yPos,zPos, 1.0f, 1.0f, 1.0f);
				break;
			case 'c':
				yPos-=INC;
				printPos();
				moveCol(xPos,yPos,zPos, 1.0f, 1.0f, 1.0f);
				break;
			case 'd':
				yPos+=INC;
				printPos();
				moveCol(xPos,yPos,zPos, 1.0f, 1.0f, 1.0f);
				break;
			case 'o':
				sendProfile();
				break;

			case '0':
				spiTx[0]=0x01<<9;
				spiTx[1]=0x0;
				spiTx[2]=0x0;
				spiTx[3]=0x0;
				spiTx[4]=0;
				transfer(8);
				break;
			case '=':
				if(timeFactor<63)
				{
					timeFactor++;
					setTimeFactor(timeFactor);
					
					printf("Time factor %d\n", timeFactor); 
				}
				break;
			case ']':
				if(timeFactor>0)
				{
					timeFactor--;
					setTimeFactor(timeFactor);
					
					printf("Time factor %d\n", timeFactor);
				}
				break;
			case 'j':
				cenX += MOVE_INC;
				moveCenter(cenX, cenY, cenZ);
				break;
			case 'm':
				cenX -= MOVE_INC;
				moveCenter(cenX, cenY, cenZ);
				break;
			case 'k':
				cenY += MOVE_INC;
				moveCenter(cenX, cenY, cenZ);
				break;
			case ',':
				cenY -= MOVE_INC;
				moveCenter(cenX, cenY, cenZ);
				break;
			case 'l':
				cenZ += MOVE_INC;
				moveCenter(cenX, cenY, cenZ);
				break;
			case '.':
				cenZ -= MOVE_INC;
				moveCenter(cenX, cenY, cenZ);
				break;	
			case '1':
				rotX += 360.0/127.0;
				if(rotX > 180.0f)
					rotX -= 360.09f;
				rotate(rotX, rotY, rotZ);
				break;
			case 'q':
				rotX -= 360.0/127.0;
				if(rotX < -180.0f)
					rotX += 360.09f;
				rotate(rotX, rotY, rotZ);
				break;
			case '2':
				rotY += 360.0/127.0;
				if(rotY > 180.0f)
					rotY -= 360.09f;
				rotate(rotX, rotY, rotZ);
				break;
			case 'w':
				rotY -= 360.0/127.0;
				if(rotY < -180.0f)
					rotY += 360.09f;
				rotate(rotX, rotY, rotZ);
				break;
			case '3':
				rotZ += 360.0/127.0;
				if(rotZ > 180.0f)
					rotZ -= 360.09f;
				rotate(rotX, rotY, rotZ);
				break;
			case 'e':
				rotZ -= 360.0/127.0;
				if(rotZ < -180.0f)
					rotZ += 360.09f;
				rotate(rotX, rotY, rotZ);
				break;
			case '4':
				scale += 0.05f;
				if(scale> 1.0f)
					scale = 1.0f;
				cenScale[0] = scale;
				cenScale[1] = scale;
				cenScale[2] = scale;
				sendMatrix();
				break;
			case 'r':
				scale -= 0.05f;
				if(scale<0.05f)
					scale = 0.05f;
				cenScale[0] = scale;
				cenScale[1] = scale;
				cenScale[2] = scale;
				sendMatrix();
				break;	
			case '5':
				BoardDistance += 0.1;
				sendHalfDistance(BoardDistance/2);
				printf("Distance: %f\n", BoardDistance);
				break;
			case 't':
				BoardDistance -= 0.1;
				sendHalfDistance(BoardDistance/2);
				printf("Distance: %f\n", BoardDistance);
				break;
			case '+':
				runFlyAround();
				break;
		}
		
	}
	
	closeSPI();
    return 0; 
} 

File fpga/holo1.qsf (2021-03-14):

# -------------------------------------------------------------------------- #
#
# Copyright (C) 2019  Intel Corporation. All rights reserved.
# Your use of Intel Corporation's design tools, logic functions 
# and other software and tools, and any partner logic 
# functions, and any output files from any of the foregoing 
# (including device programming or simulation files), and any 
# associated documentation or information are expressly subject 
# to the terms and conditions of the Intel Program License 
# Subscription Agreement, the Intel Quartus Prime License Agreement,
# the Intel FPGA IP License Agreement, or other applicable license
# agreement, including, without limitation, that your use is for
# the sole purpose of programming logic devices manufactured by
# Intel and sold by Intel or its authorized distributors.  Please
# refer to the applicable agreement for further details, at
# https://fpgasoftware.intel.com/eula.
#
# -------------------------------------------------------------------------- #
#
# Quartus Prime
# Version 18.1.1 Build 646 04/11/2019 SJ Lite Edition
# Date created = 20:35:52  January 31, 2020
#
# -------------------------------------------------------------------------- #
#
# Notes:
#
# 1) The default values for assignments are stored in the file:
#		holo1_assignment_defaults.qdf
#    If this file doesn't exist, see file:
#		assignment_defaults.qdf
#
# 2) Altera recommends that you do not modify this file. This
#    file is updated automatically by the Quartus Prime software
#    and any changes you make may be lost or overwritten.
#
# -------------------------------------------------------------------------- #


set_global_assignment -name FAMILY "Cyclone 10 LP"
set_global_assignment -name DEVICE 10CL010YE144C8G
set_global_assignment -name TOP_LEVEL_ENTITY HoloTop
set_global_assignment -name ORIGINAL_QUARTUS_VERSION 18.1.1
set_global_assignment -name PROJECT_CREATION_TIME_DATE "20:35:52  JANUARY 31, 2020"
set_global_assignment -name LAST_QUARTUS_VERSION "18.1.1 Lite Edition"
set_global_assignment -name PROJECT_OUTPUT_DIRECTORY output_files
set_global_assignment -name MIN_CORE_JUNCTION_TEMP 0
set_global_assignment -name MAX_CORE_JUNCTION_TEMP 85
set_global_assignment -name DEVICE_FILTER_PACKAGE "ANY QFP"
set_global_assignment -name DEVICE_FILTER_PIN_COUNT 144
set_global_assignment -name ERROR_CHECK_FREQUENCY_DIVISOR 1
set_global_assignment -name NOMINAL_CORE_SUPPLY_VOLTAGE 1.2V
set_global_assignment -name EDA_SIMULATION_TOOL "ModelSim-Altera (SystemVerilog)"
set_global_assignment -name EDA_TIME_SCALE "1 ps" -section_id eda_simulation
set_global_assignment -name EDA_OUTPUT_DATA_FORMAT "SYSTEMVERILOG HDL" -section_id eda_simulation
set_global_assignment -name EDA_GENERATE_FUNCTIONAL_NETLIST OFF -section_id eda_board_design_timing
set_global_assignment -name EDA_GENERATE_FUNCTIONAL_NETLIST OFF -section_id eda_board_design_symbol
set_global_assignment -name EDA_GENERATE_FUNCTIONAL_NETLIST OFF -section_id eda_board_design_signal_integrity
set_global_assignment -name EDA_GENERATE_FUNCTIONAL_NETLIST OFF -section_id eda_board_design_boundary_scan
set_global_assignment -name POWER_PRESET_COOLING_SOLUTION "23 MM HEAT SINK WITH 200 LFPM AIRFLOW"
set_global_assignment -name POWER_BOARD_THERMAL_MODEL "NONE (CONSERVATIVE)"
set_location_assignment PIN_28 -to mosi
set_location_assignment PIN_24 -to sck
set_location_assignment PIN_25 -to ncs
set_location_assignment PIN_22 -to CLK_24M576
set_instance_assignment -name RESERVE_PIN AS_INPUT_TRI_STATED -to ncs
set_instance_assignment -name RESERVE_PIN AS_INPUT_TRI_STATED -to sck
set_instance_assignment -name RESERVE_PIN AS_INPUT_TRI_STATED -to mosi
set_instance_assignment -name RESERVE_PIN AS_INPUT_TRI_STATED -to CLK_24M576
set_location_assignment PIN_52 -to t[0]
set_location_assignment PIN_53 -to t[1]
set_location_assignment PIN_54 -to t[2]
set_location_assignment PIN_55 -to t[3]
set_location_assignment PIN_58 -to t[4]
set_location_assignment PIN_59 -to t[5]
set_location_assignment PIN_60 -to t[6]
set_location_assignment PIN_65 -to t[7]
set_location_assignment PIN_66 -to t[8]
set_location_assignment PIN_67 -to t[9]
set_location_assignment PIN_68 -to t[10]
set_location_assignment PIN_69 -to t[11]
set_location_assignment PIN_70 -to t[12]
set_location_assignment PIN_71 -to t[13]
set_location_assignment PIN_72 -to t[14]
set_location_assignment PIN_73 -to t[15]
set_location_assignment PIN_74 -to t[16]
set_location_assignment PIN_75 -to t[17]
set_location_assignment PIN_76 -to t[18]
set_location_assignment PIN_77 -to t[19]
set_location_assignment PIN_80 -to t[20]
set_location_assignment PIN_83 -to t[21]
set_location_assignment PIN_84 -to t[22]
set_location_assignment PIN_85 -to t[23]
set_location_assignment PIN_87 -to t[24]
set_location_assignment PIN_98 -to t[25]
set_location_assignment PIN_99 -to t[26]
set_location_assignment PIN_100 -to t[27]
set_location_assignment PIN_101 -to t[28]
set_location_assignment PIN_103 -to t[29]
set_location_assignment PIN_105 -to t[30]
set_location_assignment PIN_106 -to t[31]
set_location_assignment PIN_111 -to t[32]
set_location_assignment PIN_112 -to t[33]
set_location_assignment PIN_113 -to t[34]
set_location_assignment PIN_114 -to t[35]
set_location_assignment PIN_115 -to t[36]
set_location_assignment PIN_119 -to t[37]
set_location_assignment PIN_120 -to t[38]
set_location_assignment PIN_121 -to t[39]
set_location_assignment PIN_124 -to t[40]
set_location_assignment PIN_125 -to t[41]
set_location_assignment PIN_126 -to t[42]
set_location_assignment PIN_127 -to t[43]
set_location_assignment PIN_128 -to t[44]
set_location_assignment PIN_129 -to t[45]
set_location_assignment PIN_132 -to t[46]
set_location_assignment PIN_133 -to t[47]
set_location_assignment PIN_135 -to t[48]
set_location_assignment PIN_136 -to t[49]
set_global_assignment -name PARTITION_NETLIST_TYPE SOURCE -section_id Top
set_global_assignment -name PARTITION_FITTER_PRESERVATION_LEVEL PLACEMENT_AND_ROUTING -section_id Top
set_global_assignment -name PARTITION_COLOR 16764057 -section_id Top
set_instance_assignment -name IO_STANDARD "3.0-V LVTTL" -to CLK_24M576
set_instance_assignment -name IO_STANDARD "3.0-V LVTTL" -to mosi
set_instance_assignment -name IO_STANDARD "3.0-V LVTTL" -to ncs
set_instance_assignment -name IO_STANDARD "3.0-V LVTTL" -to sck
set_instance_assignment -name IO_STANDARD "3.0-V LVTTL" -to t[0]
set_instance_assignment -name IO_STANDARD "3.0-V LVTTL" -to t[1]
set_instance_assignment -name IO_STANDARD "3.0-V LVTTL" -to t[2]
set_instance_assignment -name IO_STANDARD "3.0-V LVTTL" -to t[3]
set_instance_assignment -name IO_STANDARD "3.0-V LVTTL" -to t[4]
set_instance_assignment -name IO_STANDARD "3.0-V LVTTL" -to t[5]
set_instance_assignment -name IO_STANDARD "3.0-V LVTTL" -to t[6]
set_instance_assignment -name IO_STANDARD "3.0-V LVTTL" -to t[7]
set_instance_assignment -name IO_STANDARD "3.0-V LVTTL" -to t[8]
set_instance_assignment -name IO_STANDARD "3.0-V LVTTL" -to t[9]
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

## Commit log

2021-03-14 second commit
    [FPGA.sch, LED mount1.stl, LED.sch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]
2021-03-25 updated board readme
